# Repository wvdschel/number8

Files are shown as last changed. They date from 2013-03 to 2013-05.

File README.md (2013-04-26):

number8
=======

Number8 is the second iteration of our [WELEK robot sumo competition](http://ieeesb.elis.ugent.be/nl/welek/robot/2013) entry.
It is a differential wheeled robot, built out of Lego Technics and powered by 5 Lego Technic motors and a PIC18.

It is equiped with 8 input sources:

1. 2x analog infrared distance sensors on the front
2. 4x analog color sensors on the bottom, one on each corner of the robot, to detect the edge of the arena
3. 1x digital pressure sensor on the back, to detect an attack from behind (this sensor is colloqually referred to as "the butt-sex-detector").
4. 1x rotary encoder to measure our forward/backward movement

Media
-----

[A video featuring our first build, number7](http://www.youtube.com/embed/BkIkCT7gmbQ). It is the robot with double batteries and green-grey scoop. It is also the only robot consistently winning throughout the video, and the only one that does not recieve human help ;)

Since then, we have made the robot faster (a gear ratio change, resulting in a 9 times faster robot, at the cost of a 9 times lower torque).

We also replaced the scoop, since it was mechanically flawed and it on multiple occasions resulted in our robot being lifted off the ground with all but its last wheels. It now has a bumper made of wheels constantly pushing the enemy away.

The progress wheel was also not present in the first version.

Operating instructions
----------------------

As per the contest rules, the robot operates autonomously during combat. The only operations a meatbag assistant should perform is to start the robot. This is done as follows:

1. Put the robot down inside the arena. Make sure all corner sensors are inside the arena, and not on or over the edge. Also make sure that nothing is in front of the robot, since that would mess up the initial sensor calibration in the next step.
2. Press any button on the Dwengo board to calibrate the sensors. Whatever is under the ground sensors will be considered as the color of the arena, and the distance sensor values will be considered "infinite distance" values.
3. Press the north or south buttons to start the robot in forward drive mode, or left or right to have it perform a flanking operation.
4. Watch it destroy the competition.

Code
----
We started from a modified version of the "sumolib" provided by the contest organization. We modified it to use our motor controller and to print to serial instead of the LCD.

Most of the logic is contained in aiLib.c. The robot operates as a state machine, switching between a search state, a destroy state, a flanking state and a survival state based on its sensor readings. Transitions can easily be found by searching for `SWITCH_STATE`.

The `sumolib` directory contains the modified version of the sumolib we use, while `quadenclib` contains code we plucked off the internet (TODO: add link) for using our rotary encoder.

Debugging
---------

There are two debugging methods available: serial prints and LEDs 4 trough 7 on the Dwengo board.

### Serial debugging
Serial debugging is enabled by setting `DEBUG` to `1` in `serialDebug.h`.

Since the motor controller is being operated over serial as well, we also have some garbage from the motor commands on the serial, and we can't print high bytes.

### LED debugging
The four last LEDs of the Dwengo board indicate the state the robot is in:

	 LD7 LD6 LD5 LD4 LD3 LD2 LD1 LD0
	/-------------------------------\
	| o   o   o   o   o   o   o   o |
	\-------------------------------/
	  |   |   |   |       |   |_ Rotary encoder feedback
	  |   |   |   |       |_____ Rotary encoder feedback
	  |   |   |   |_____________ Flashes when a stall is detected
	  |   |   |_________________ STATE_SEEK
	  |   |_____________________ STATE_DESTROY
	  |_________________________ STATE_SURVIVE

If both LD5 and LD6 are lit, the robot is in `STATE_FLANK`.

Component references
--------------------

Rotary encoder: [Sparkfun - COM-09117](https://www.sparkfun.com/products/9117)
Long range sensors: [Sharp GP2Y0A21YK0F](http://ieeesb.elis.ugent.be/sites/ieeesb.elis.ugent.be/files/gp2y0a21yk_e.pdf)
Ground sensors: [Vishay TCRT5000](http://ieeesb.elis.ugent.be/sites/ieeesb.elis.ugent.be/files/tcrt5000.pdf)

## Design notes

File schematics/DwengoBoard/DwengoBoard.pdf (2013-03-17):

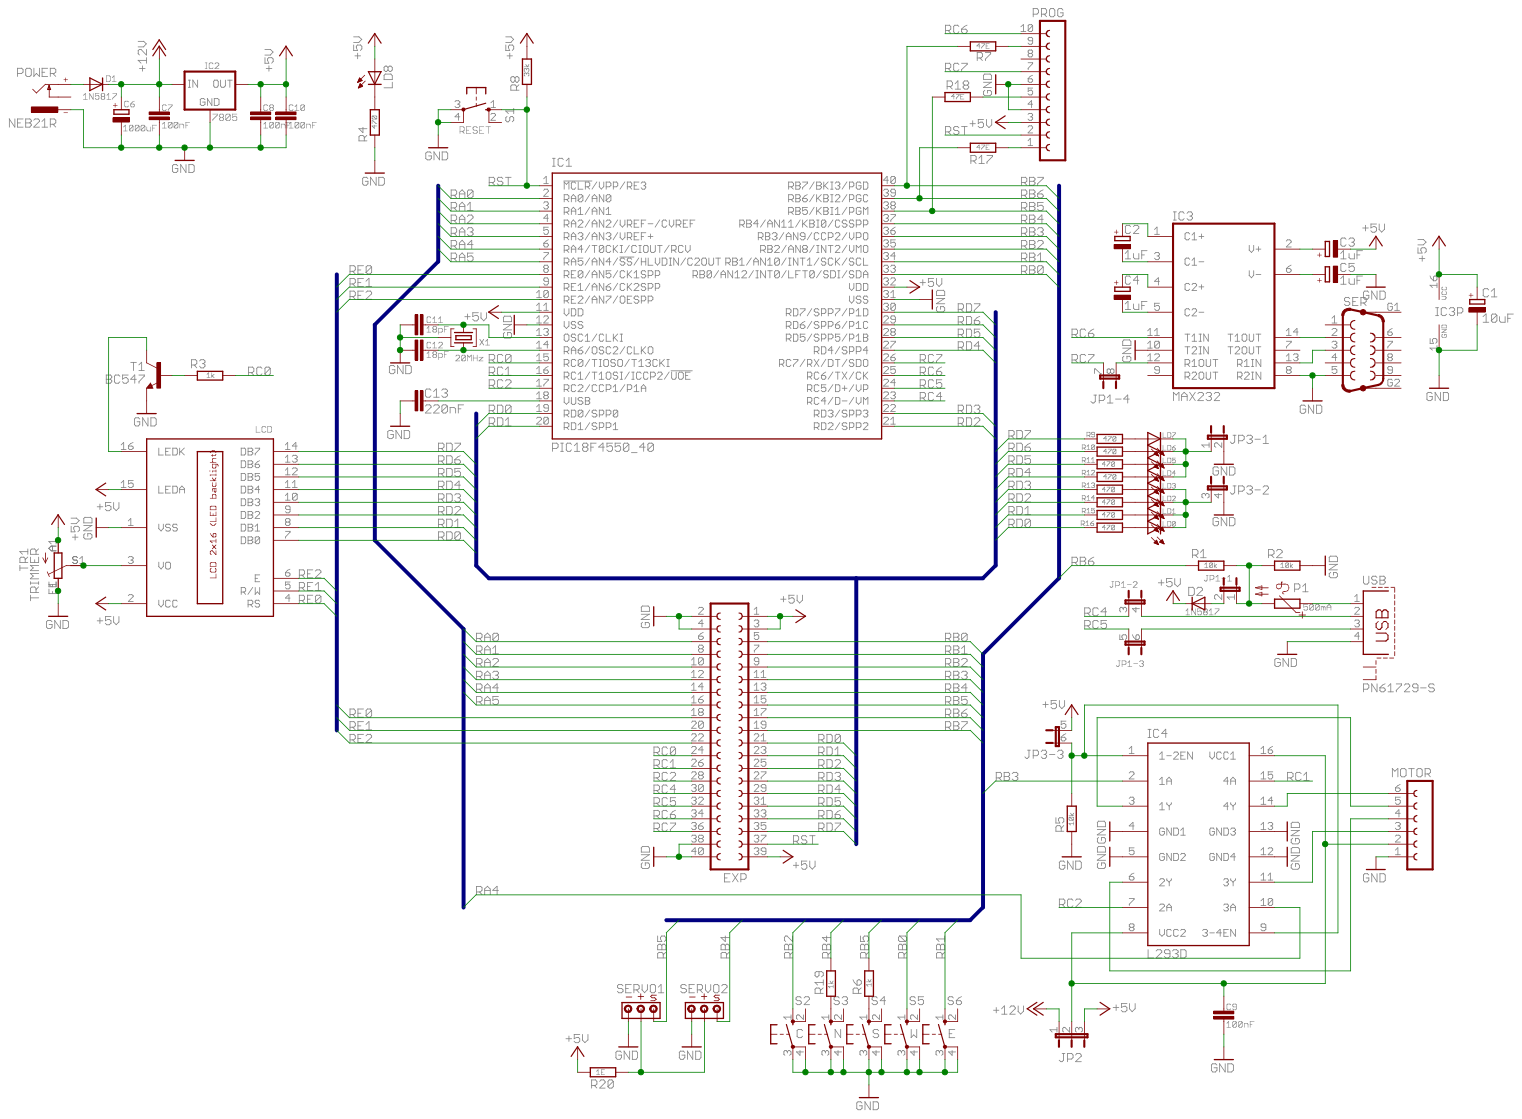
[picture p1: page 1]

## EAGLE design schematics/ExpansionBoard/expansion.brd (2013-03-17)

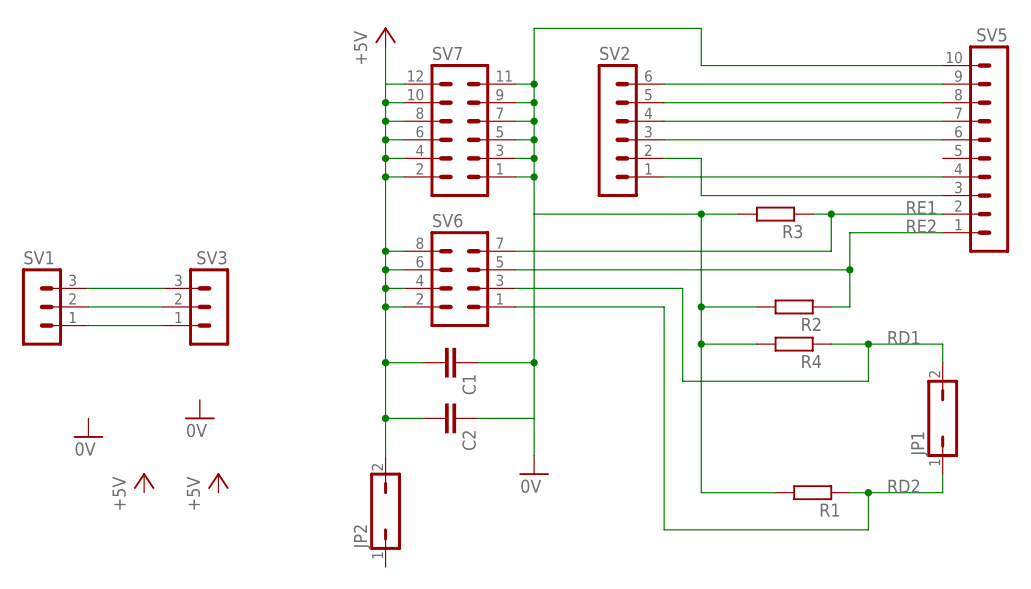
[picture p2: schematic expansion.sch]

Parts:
C1, C2: C-EU025-030X050; C025-030X050
JP1, JP2: JP1Q; JP1
R1: R-EU_0207/10; 0207/10
R2: R-EU_0207/5V; 0207/5V
R3: R-EU_0207/2V; 0207/2V
R4: R-EU_0204/7; 0204/7
SV1, SV3: MA03-1
SV2: MA06-1
SV5: MA10-1
SV6: MA04-2
SV7: MA06-2

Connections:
0V: C1.1, C2.1, R1.2, R2.2, R3.2, R4.2, SV5.10, SV7.1, SV7.3, SV7.5, SV7.7, SV7.9, SV7.11
+5V: C1.2, C2.2, JP2.2, SV6.2, SV6.4, SV6.6, SV6.8, SV7.2, SV7.4, SV7.6, SV7.8, SV7.10, SV7.12
unnamed: SV2.6, SV5.9
unnamed: SV2.5, SV5.8
unnamed: SV2.4, SV5.7
unnamed: SV2.3, SV5.6
unnamed: SV1.3, SV3.3
unnamed: SV1.2, SV3.2
unnamed: SV1.1, SV3.1
unnamed: SV2.1, SV5.4
unnamed: SV2.2, SV5.3
RD1: JP1.2, R4.1, SV6.3
RD2: JP1.1, R1.1, SV6.1
RE1: R3.1, SV5.2, SV6.7
RE2: R2.1, SV5.1, SV6.5

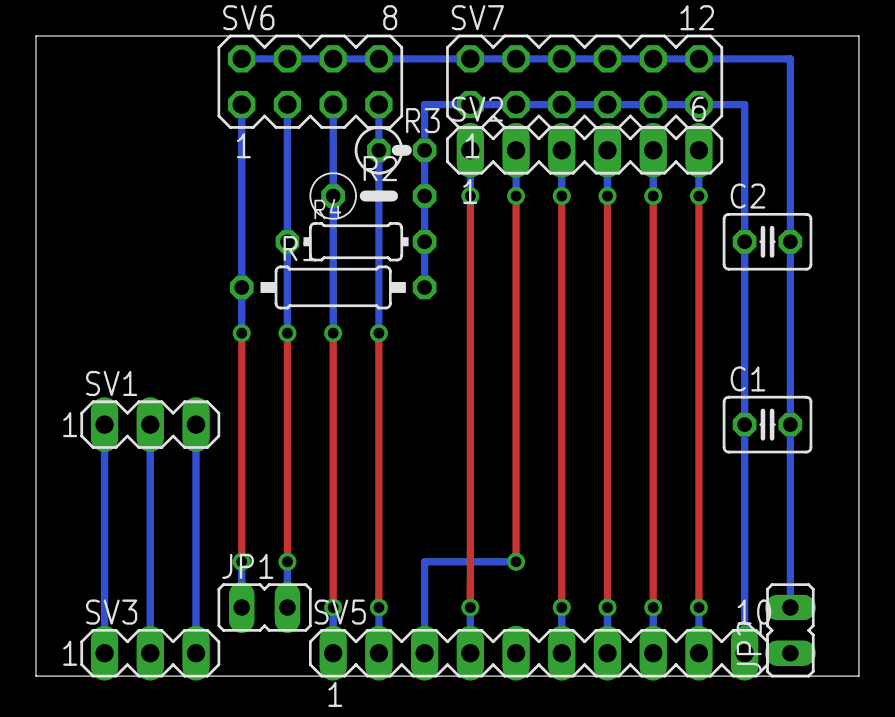
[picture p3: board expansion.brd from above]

Board: 2 copper layers, 45.7 x 35.6 mm, 14 parts (0 on the bottom side), 15 nets.

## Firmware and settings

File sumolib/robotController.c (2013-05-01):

/**
 * Robot Framework
 * uses Dwengo-library (www.dwengo.org)
 * 
 * Start from this framework to program your own intelligent robot
 * IMPORTANT: if (old) WELEK board is used add Project > Build Option > Project > MPLAB C18 macro WELEK
 *
 * Version: 1.4 (modified for WELEK sumo robot competition)
 * Date: 15-02-2011
 * (c) Francis wyffels
 */

#define NO_LCD

#include <p18f4550.h>			// include p18f4455 library
#include <stdlib.h>
#include <usart.h>
#include "dwengoBoard.h"
#include "dwengoConfig.h"
#include "dwengoMotor.h"
#include "dwengoADC.h"
#include "dwengoDelay.h"
//#include "dwengoLCD.h"
#include "aiLib.h"
#include "serialDebug.h"

// put your macro's here
#define MAX_TIMER_SERVO 64536 // maximal servo left position: DO NOT EDIT THIS
#define MIN_TIMER_SERVO 62086 // maximal servo right position: DO NOT EDIT THIS

// interrupt handlers
void YourHighPriorityISRCode();
void YourLowPriorityISRCode();

// initalization of USART
void initUsart(void);

// global variables
unsigned int timerServo;	// determines position of servo DO NOT EDIT

// Bootloader occupy addresses 0x00-0x1FFF and thus cannot be used.
// Addresses 0x00, 0x08 and 0x18 have to be remapped
extern void _startup(void);
#pragma code REMAPPED_RESET_VECTOR = 0x2000
void _reset(void) {
	_asm
		goto _startup
	_endasm
}

#pragma code REMAPPED_HIGH_INTERRUPT_VECTOR = 0x2008
void Remapped_High_ISR(void) {
	_asm
		goto YourHighPriorityISRCode
	_endasm
}

#pragma code REMAPPED_LOW_INTERRUPT_VECTOR = 0x2018
void Remapped_Low_ISR(void) {
	_asm
		goto YourLowPriorityISRCode
	_endasm
}

// mapping interrupt vectors
#pragma code high_vector=0x08
void high_vector() {
	_asm
		goto 0x2008
	_endasm
}
#pragma code

#pragma code low_vector=0x18
void low_vector() {
	_asm
		goto 0x2018
	_endasm
}
#pragma code

// interrupt handler routines DO NOT EDIT
#pragma interrupt YourHighPriorityISRCode
void YourHighPriorityISRCode() {
#ifdef SERVO
  if(PIR1bits.TMR1IF == TRUE) {	// check interrupt flag: from timer?
    if(PORTBbits.RB5 == 0) {
      TMR1H = (timerServo & 0xFF00) >> 8; // keep most significant byte
      TMR1L = timerServo & 0x00FF; // keep least significant byte
      PORTBbits.RB5 = 1; // high pulse
    } else {
      TMR1H = 0x8A;	// timer 1 interrupt after 83.333ns*8*(65536-35536) = +/- 20ms
      TMR1L = 0xD0;	// 35536 = 0x8AD0
      PORTBbits.RB5 = 0; // low pulse
    }
    PIR1bits.TMR1IF = FALSE; // reenable TMR1 interrupt
  }
#else
  ailib_isr();
#endif
}

#pragma interruptlow YourLowPriorityISRCode
void YourLowPriorityISRCode() {

}

void main(void) {
	BYTE started = FALSE;
	int sensor[3];
	int i;
	// add your own variables here: EDIT

	// start of initializations: DO NOT EDIT
	initBoard();
	initADC();
	initMotors();
	backlightOn();
	stopMotors();
	delay_ms(10);	// wait a bit after initialisation
	// end of initializations

	// start procedure necessary for the robot competition: DO NOT EDIT
	// robot has to move to the control loop when pressing switch S (new version) or S4 (old version)
	initLCD();
	clearLCD();

	appendStringToLCD("Press center key to calibrate sensors (" __TIME__ ")");

	while(1) {
		stopMotors();
		if(SW_C == PRESSED) {
			LEDS = 0xFF;
			ailib_init();
			break;
		} else {
			delay_ms(50);
		}
	}
	delay_ms(300);
	LEDS = 0;

	appendStringToLCD("(S)tart me");
	while(!started) {
		stopMotors();
		if(SW_N == PRESSED || SW_S == PRESSED) {
			initState(DIR_FORWARD);
			started = TRUE;
		} else if(SW_E == PRESSED) {
			initState(DIR_LEFT);
			started = TRUE;
		} else if(SW_W == PRESSED) {
			initState(DIR_RIGHT);
			started = TRUE;
		} else {
			delay_ms(50);
		}
	}
	// ~5 seconds waiting
	clearLCD();
	appendStringToLCD("Start counting");
	LEDS = 0;
	for(i=0;i<5;i++) {
		LEDS *= 2;
		LEDS += 1;
		delay_ms(920);
	} // end of starting procedure
	clearLCD();

#ifdef SERVO
	// routines for servo control DO NOT EDIT
	// servo pins
	INTCON2bits.NOT_RBPU = 1; // disable internal pull-ups: SWITCHES WON'T WORK ANYMORE
  	TRISBbits.TRISB5 = 0; // set RB5 as output
  	PORTBbits.RB5 = 0; // initialize with 0

  	// Timer 1 interrupt example, control one servo on pin RD0
  	// timings servo has to be within 0.7 ms up to 2.3 ms
  	// 0.7 ms: timer 1 interrupt after 83.333ns*8*(65536-64536) = 0.7ms (64486 = 0xFBE6)
  	// 2.3 ms: timer 1 interrupt after 83.333ns*8*(65536-62086) = 2.3ms (62086 = 0xF286)
  	timerServo = MIN_TIMER_SERVO; // in left position
  	PIR1bits.TMR1IF = 0;
  	RCONbits.IPEN = 1;
  	RCONbits.SBOREN = 0;	// BOR = off
  	TMR1H = (timerServo & 0xFF00) >> 8; // keep most significant byte
  	TMR1L = timerServo & 0x00FF; // keep least significant byte
  	T1CON = 0b00110001; // 48Mhz/4, prescaler 1/8
  	INTCONbits.GIEH = TRUE; // GIEH = TRUE
  	IPR1bits.TMR1IP = 1;
	PIE1bits.TMR1IE = 1;
	// end of servo control routines
#endif

	/********************** MODIFY CODE STARTING FROM HERE ***********************/
	// Write your controller inside this while-loop: YOU HAVE TO EDIT THIS
	ailib_init();
	while(TRUE) { // do forever
		doMove();
	}
}

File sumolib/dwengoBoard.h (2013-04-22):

/*
 *  dwengoBoard.h
 *  
 *
 *
 */

#ifndef DWENGO_BOARD_H
#define DWENGO_BOARD_H

// Constants
#define TRUE    1
#define FALSE   0
#define HIGH    1
#define LOW     0
#define PRESSED 0
#define INPUT   1
#define OUTPUT  0

// Data types
#define BYTE unsigned char

// Pin assignments

// leds
#define LEDS                PORTD
#define LEDS_DIR            TRISD
#define LED0                PORTDbits.RD0
#define LED1                PORTDbits.RD1
#define LED2                PORTDbits.RD2
#define LED3                PORTDbits.RD3
#define LED4                PORTDbits.RD4
#define LED5                PORTDbits.RD5
#define LED6                PORTDbits.RD6
#define LED7                PORTDbits.RD7

// buttons
#if defined(WELEK)
  #define SW_C                PORTBbits.RB0
  #define SW_C_DIR            TRISBbits.TRISB0
  #define SW_N                PORTBbits.RB4
  #define SW_N_DIR            TRISBbits.TRISB4
  #define SW_E                PORTBbits.RB7
  #define SW_E_DIR            TRISBbits.TRISB7
  #define SW_S                PORTBbits.RB5
  #define SW_S_DIR            TRISBbits.TRISB5
  #define SW_W                PORTBbits.RB6
  #define SW_W_DIR            TRISBbits.TRISB6
#else
  #define SW_C                PORTBbits.RB2
  #define SW_C_DIR            TRISBbits.TRISB2
  #define SW_N                PORTBbits.RB4
  #define SW_N_DIR            TRISBbits.TRISB4
  #define SW_E                PORTBbits.RB1
  #define SW_E_DIR            TRISBbits.TRISB1
  #define SW_S                PORTBbits.RB5
  #define SW_S_DIR            TRISBbits.TRISB5
  #define SW_W                PORTBbits.RB0
  #define SW_W_DIR            TRISBbits.TRISB0
#endif

// LCD display
#define LCD_DATA            PORTD 
#define LCD_DATA_DIR        TRISD
#define LCD_BACKLIGHT       PORTCbits.RC0
#define LCD_BACKLIGHT_DIR   TRISCbits.TRISC0
#define LCD_RW              PORTEbits.RE1
#define LCD_RW_DIR          TRISEbits.TRISE1
#define LCD_RS              PORTEbits.RE0
#define LCD_RS_DIR          TRISEbits.TRISE0
#define LCD_EN              PORTEbits.RE2
#define LCD_EN_DIR          TRISEbits.TRISE2

// servo connectors
#define SERVO1              PORTBbits.RB5
#define SERVO1_DIR          TRISBbits.TRISB5
#define SERVO2              PORTBbits.RB4
#define SERVO2_DIR          TRISBbits.TRISB4

// motor driver
#if defined(WELEK)
  #define MOTOR1_0            PORTCbits.RC2
  #define MOTOR1_0_DIR        TRISCbits.TRISC2
  #define MOTOR1_1            PORTBbits.RB2
  #define MOTOR1_1_DIR        TRISBbits.TRISB2
  #define MOTOR2_0            PORTCbits.RC1
  #define MOTOR2_0_DIR        TRISCbits.TRISC1
  #define MOTOR2_1            PORTBbits.RB3
  #define MOTOR2_1_DIR        TRISBbits.TRISB3
#else
  #define MOTOR1_0            PORTCbits.RC2
  #define MOTOR1_0_DIR        TRISCbits.TRISC2
  #define MOTOR1_1            PORTAbits.RA4
  #define MOTOR1_1_DIR        TRISAbits.TRISA4
  #define MOTOR2_0            PORTCbits.RC1
  #define MOTOR2_0_DIR        TRISCbits.TRISC1
  #define MOTOR2_1            PORTBbits.RB3
  #define MOTOR2_1_DIR        TRISBbits.TRISB3
#endif

// include libraries
#include <p18f4550.h>
#include "sumolib/dwengoDelay.h"

//#ifndef NO_LCD
#include "sumolib/dwengoLCD.h"
//#endif

// intialisation routine for the board
void initBoard(void);

#endif //DWENGO_BOARD_H

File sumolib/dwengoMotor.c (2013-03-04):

/**
 * Motor driver
 * part of Dwengo library
 * 
 * Control of motor driver on the Dwengo board
 *
 * Version: 1.0.$Revision: 1644 $
 * Date: $Date: 2010-01-11 20:17:26 +0100 (ma, 11 jan 2010) $
 * (c) Dwengo vzw - http://www.dwengo.org
 */

// wait time to minimize transients in the motors when introducing abrupt speed changes, in ms
#define TRANSIENT_DELAY 20

#include <pwm.h>
#include <timers.h>

#include "dwengoBoard.h"
#include "dwengoMotor.h"
#include "dwengoDelay.h"


void initMotors() {
  // Set the motor outputs as digital output
  MOTOR1_0_DIR = 0;
  MOTOR1_1_DIR = 0;
  MOTOR2_0_DIR = 0;
  MOTOR2_1_DIR = 0;
  
  // Maximal PWM freq: 5000Hz (using L293DNE motor driver)
  // PWM period = (0xFF + 1)*4*Tosc*T2Prescaler
  OpenPWM1(0xFF);   // configuring PWM module 1
  OpenPWM2(0xFF);   // configuring PWM module 2
  
  // Configuring timer 2 which provides timing for PWM
  // TIMER_INT_OFF: disable timer interrupt
  // T2_PS_1_4: Timer2 prescaling set to 4
  // T2_POST_1_1: Timer2 postscaling set to 1
  OpenTimer2(TIMER_INT_OFF & T2_PS_1_4 & T2_POST_1_1);
}

void setSpeedMotor1(short speed) {
  static BYTE prev_dir;
  BYTE dir;
  dir = (speed > 0);
  
  // check if motor has changed direction
  if (dir != prev_dir) {
    // stop motor
    SetDCPWM1(0);
    // wait a short time
    delay_ms(TRANSIENT_DELAY);
    // update direction
    prev_dir = dir;
  }

  if (dir == FORWARD) {
    SetDCPWM1(speed);
    MOTOR1_1 = 0;
  } 
  else { // speed is negative
    SetDCPWM1(1023+speed);
    MOTOR1_1 = 1;
  }
}

void setSpeedMotor2(short speed) {
  static BYTE prev_dir;
  BYTE dir;
  dir = (speed > 0);
  
  // check if motor has changed direction
  if (dir != prev_dir) {
    // stop motor
    SetDCPWM2(0);
    // wait a short time
    delay_ms(TRANSIENT_DELAY);
    // update direction
    prev_dir = dir;
  }
  
  if (dir == FORWARD) {
    SetDCPWM2(speed);
    MOTOR2_1 = 0;
  } 
  else { // speed is negative
    SetDCPWM2(1023+speed);
    MOTOR2_1 = 1;
  }
}

void stopMotors() {
  SetDCPWM1(0);
  MOTOR1_1 = 0;
  
  SetDCPWM2(0);
  MOTOR2_1 = 0;
}

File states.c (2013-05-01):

#include "states.h"
#include "aiLib.h"
#include "serialDebug.h"

#define DISTANCE_CLOSE		(int)900	// Anything lower than this value is considered close enough to attack, anything higher is considered too far away
#define DISTANCE_VERY_CLOSE	(int)780	// This is close enough to ignore the white lines

#define SEEK_ROTATE_TIME 	(int)80 	// How many iterations should we wait before moving the robot to change the search space.
							 			// To disable this and just turn left all the time, set to 0.
#define SEEK_MOVE_DISTANCE	(int)50		// How long the robot should move forward before looking around again.
#define MIN_PROGRESS		(int)2		// Minimal progress to continue pushing during an attack
#define SURVIVE_CLEARANCE	(int)30		// Minimal progress before leaving survival

#define FLANK_ROTATE_TIME	(int)30
#define FLANK_BACK_DISTANCE	(int)-4
#define FLANK_REAR_DISTANCE	(int)18
#define FLANK_REAR_TIME		(int)25

#define MAX_SPEED			(int)1023
#define SAFE_SPEED			(int)800
#define VERY_SAFE_SPEED		(int)650
//#define SAFE_SPEED			(int)0
#define SCAN_SPEED			(int)800
//#define SCAN_SPEED			(int)0

// Check if we see a white line, and switch to survival state if we do.
int survivalCheck()
{
	if(groundSensor(DIR_FORWARD | DIR_LEFT) || groundSensor(DIR_FORWARD | DIR_RIGHT)
		|| groundSensor(DIR_BACK | DIR_LEFT) || groundSensor(DIR_BACK | DIR_RIGHT))
	{
		SWITCH_STATE(STATE_SURVIVE);
		return TRUE;
	}
	return FALSE;
}

// Check if we detect an enemy (front or rear), and switch state accordingly
int enemyCheck(int distanceLeft, int distanceRight)
{
	// If something is close, assume there's an enemy in front
	if(distanceLeft < DISTANCE_CLOSE || distanceRight < DISTANCE_CLOSE)
	{
		if(currState != STATE_ATTACK)
			SWITCH_STATE(STATE_ATTACK);
		return TRUE;
	}
	// If our rear is pressed, there's probably an enemy in the back
	if(pushSensor(DIR_BACK))
	{
		if(currState != STATE_ATTACK_REAR)
			SWITCH_STATE(STATE_ATTACK_REAR);
		setMotors(0, 0);
		return TRUE;
	}
	return FALSE;
}

static int edgeDetectedCount = 0;
void doMoveState()
{
	int distanceLeft, distanceRight, distanceAvg;

	distanceLeft = distanceSensor(DIR_LEFT);
	distanceRight = distanceSensor(DIR_RIGHT);
	distanceAvg = (distanceLeft + distanceRight) / 2;

	if(enemyCheck(distanceLeft, distanceRight) || survivalCheck())
	{
		return;
	}

	// Reset our edge-vision counter when we start moving
	if(stateTimer == 1)
	{
		edgeDetectedCount = 0;
		//setMotors(DIR_FORWARD, MAX_SPEED);
		setMotors(DIR_FORWARD, SAFE_SPEED);
	}
	// If we (probably) see a ledge, increment the counter, if not, reset the counter
	if(distanceLeft >= 1044)
	{
		edgeDetectedCount++;
	} else {
		edgeDetectedCount = 0;
	}
	// If we (think we) see the edge, slow down.
	if(edgeDetectedCount >= 3)
	{
		setMotors(DIR_FORWARD, VERY_SAFE_SPEED);
	} else {
		//setMotors(DIR_FORWARD, MAX_SPEED);
		setMotors(DIR_FORWARD, SAFE_SPEED);
	}
	// If we've covered enough distance, then go back to scanning
	if(stateProgress >= SEEK_MOVE_DISTANCE)
	{
		SWITCH_STATE(STATE_SCAN);
		return;
	}
}

void doScanState()
{
	int distanceLeft, distanceRight, distanceAvg;

	distanceLeft = distanceSensor(DIR_LEFT);
	distanceRight = distanceSensor(DIR_RIGHT);
	distanceAvg = (distanceLeft + distanceRight) / 2;

	if(enemyCheck(distanceLeft, distanceRight) || survivalCheck())
	{
		return;
	}

	setMotors(DIR_LEFT, SCAN_SPEED);

	if(stateTimer >= SEEK_ROTATE_TIME)
	{
		SWITCH_STATE(STATE_MOVE);
		return;
	}
}

static int straightAheadTime = 0;
void doAttackState()
{
	int distanceLeft, distanceRight, distanceAvg;
	if(stateTimer == 1)
		straightAheadTime = 0;

	distanceLeft = distanceSensor(DIR_LEFT);
	distanceRight = distanceSensor(DIR_RIGHT);
	distanceAvg = (distanceLeft + distanceRight) / 2;

#ifdef PROGRESS_WHEEL
	// Once we have filled up the history, and our combined progress is insufficient, consider flanking
	if(progress < MIN_PROGRESS && straightAheadTime > PROGRESS_HISTORY_SIZE)
	{
		SWITCH_STATE(STATE_FLANK_TURN);
		return;
	}
#endif
	if(distanceLeft > DISTANCE_CLOSE && distanceRight > DISTANCE_CLOSE)
	{
		// Target lost, go back to searching
		SWITCH_STATE(STATE_SCAN);
		return;
	}
	if(distanceLeft > DISTANCE_CLOSE || distanceRight > DISTANCE_CLOSE)
	{
		straightAheadTime = 0;
		// Sensors are appart, reallign.
		if(distanceLeft > distanceRight)
			setMotors(DIR_FORWARD | DIR_RIGHT, MAX_SPEED);
		else
			setMotors(DIR_FORWARD | DIR_LEFT, MAX_SPEED);
	}
	else if(distanceAvg > DISTANCE_VERY_CLOSE)
	{
		// Target straight ahead but not very close
		if(survivalCheck())
			return;
		straightAheadTime++;
		setMotors(DIR_FORWARD, SAFE_SPEED);
	} 
	else
	{
		// Target straight ahead and very close
		straightAheadTime++;
		setMotors(DIR_FORWARD, MAX_SPEED);
	}
	return;
}
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

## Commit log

2013-03-17 - added schematics - added initial code to support progress wheel - refactored some code - removed some unnecessary files
    [expansion.brd, expansion.sch]
2013-03-18 added modified version of quadrature encoder for progress wheel (http://www.pavius.net/2010/02/rotary-encoder-based-cooking-timer/)
2013-03-22 -added main microcontroller datasheet -modified quadrature encoder code for our specific extension board
2013-04-18 Added progress wheel readout to sensor readings.
2013-04-19 Motors have been swapped during reconstruction.
    I fixed the code accordingly.
    [aiLib.c]
2013-04-19 Support for black edge white arena.
    Also adjusted the timings for the faster gear ratio to not go completely
    beserk.
2013-04-19 Bugfix in initial ground sensor debug print.
    [aiLib.c]
2013-04-19 Rear and front left ground sensors were swapped.
    [aiLib.c]
2013-04-19 Made survive-mode last longer to handle high speed
    With the new gear ratio, the robot sometimes goes over the edge of the
    arena with the front sensors before going into survival mode. Because of
    the short duration of the survival mode, the robot is not able to break
    and alter direction for long enough to back up to the arena edge.
    This caused the robot to halt briefly after crossing the line, before
    continuing on its way out of the arena.
    [aiLib.c]
2013-04-21 Stop pushing if the progress wheel says we're not making progress.
    Additionally, the progress variable now reports positive values for
    forward movement, and negative values for backward movement.
2013-04-21 Removed DESTROY_OVER state and added FLANK state.
    Also modified distance sensor values to have a wider range and hopefully
    higher accuracy.
2013-04-21 Fixed LED state indication and slowed down debug mode.
    [aiLib.c]
2013-04-21 Seperated sensor calibration and robot startup
    First keypress calibrates sensors, second keypress starts the robot.
2013-04-21 Added scrolling window history for progress wheel measurements, since 15ms isn't a very meaningful sample rate.
2013-04-21 Added rotary encoder link to readme
2013-04-21 Added LED feedback for sensor calibration success
2013-04-21 Modified state LED update to preserve non-state LEDS
2013-04-22 Made project build without hardcoded library folders.
    [expansion.brd, expansion.sch]
2013-04-23 Made rear pressure sensor halt the robot while pressed.
2013-04-23 Fixed formatting of initial ground sensor prints.
    [aiLib.c]
2013-04-23 Made sensor calibration only use the center button.
2013-04-23 Changed print format, and only print progress window every 100 turns.
2013-04-24 Removed motor debug prints to prevent UART spam
    [motorController.c]
2013-04-24 Reduced progress wheel history windows size.
2013-04-24 Fixed off-by-one bug for forward motion on the progress wheel
    [aiLib.c]
2013-04-26 Added sensor spec links
2013-04-26 reordered sensors
2013-04-26 Rewrote driveUntilWhite to log long distance sensors
2013-04-26 parse ground sensor states
2013-04-27 Enabled motors
2013-04-27 Added tests for braking using only long distance sensors & initial PoC code for flanking manouver
2013-04-28 Added unused printBase64 function
2013-04-28 Removed 'EXTERMINATE' print at startup
2013-04-28 Compressed state prints for lower latency and allowing more frequent prints
2013-04-28 Updated log parser to allow reading of new print format.
2013-04-29 Fixed syntax error in input parsing
    [Main.java]
2013-04-29 Removed push sensor from survivalCheck
2013-04-29 Fixed chatter on UART by motor codes
    [aiLib.c]
2013-04-29 fixed gui after Wim's changes
    [Main.java]
2013-05-01 Swapped rear sensors
